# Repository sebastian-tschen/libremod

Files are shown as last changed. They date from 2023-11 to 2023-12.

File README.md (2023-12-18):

# Grind By Weight for Eureka MCI coffee grinder

<p align="center">
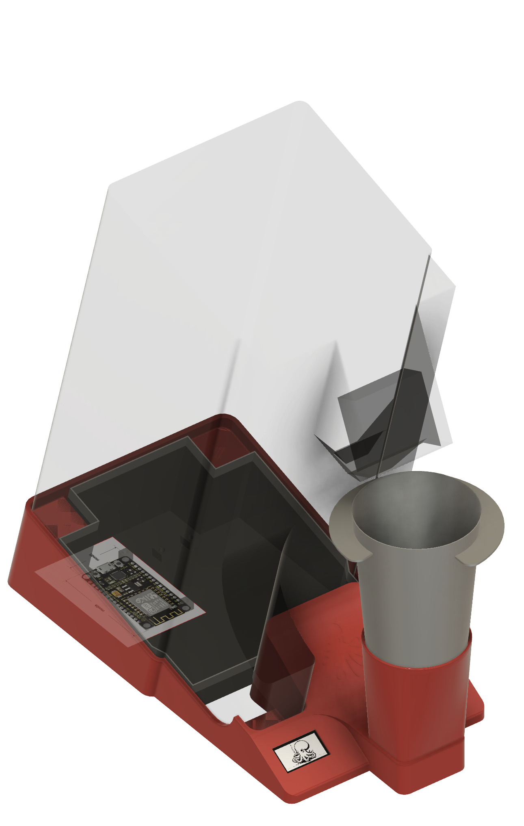
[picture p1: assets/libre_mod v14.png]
  
</p>

This project is based on [the work by Guillaume Besson](https://besson.co/projects/coffee-grinder-smart-scale). I modified it to work with my slightly different grinder and a single core ESP8266 instead of a multi-core ESP32 and added some features to the software

Bill of Material:
-----------------

- Loadcell (mine was 50x10x6mm up to 500g)
- HX711 Load Cell amplifier
- ESP8266 Dev-Board
- 0.96 inch OLED SSD1306 Display
- 4 Cylinder Magnets (6mmx6mm)
- 3D-Printed Parts

### Original electronics of the Eureca MCI

The original electronics slightly differ from the one used bt Guillaume. Mostly the microcontroller operates on a 3.3V instead of 5V. Also, most useful in and outputs where not conviniently accessible via a pinheader.

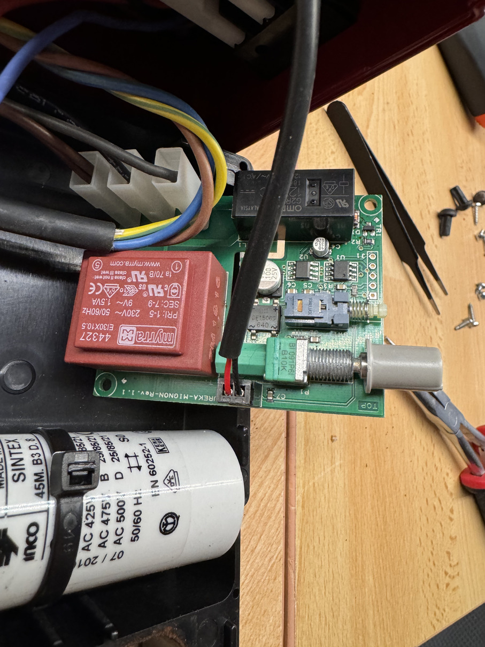
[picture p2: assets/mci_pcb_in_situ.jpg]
Original PCB in-situ


*Original PCB in-situ*

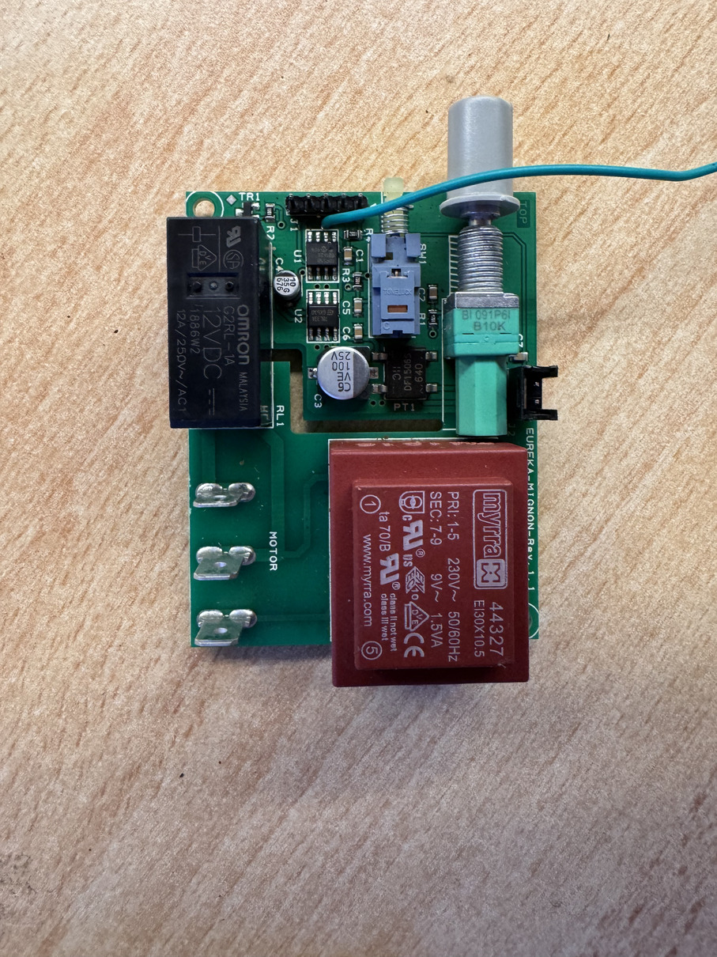
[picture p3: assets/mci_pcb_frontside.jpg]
Original PCB front side


*Original PCB front side*

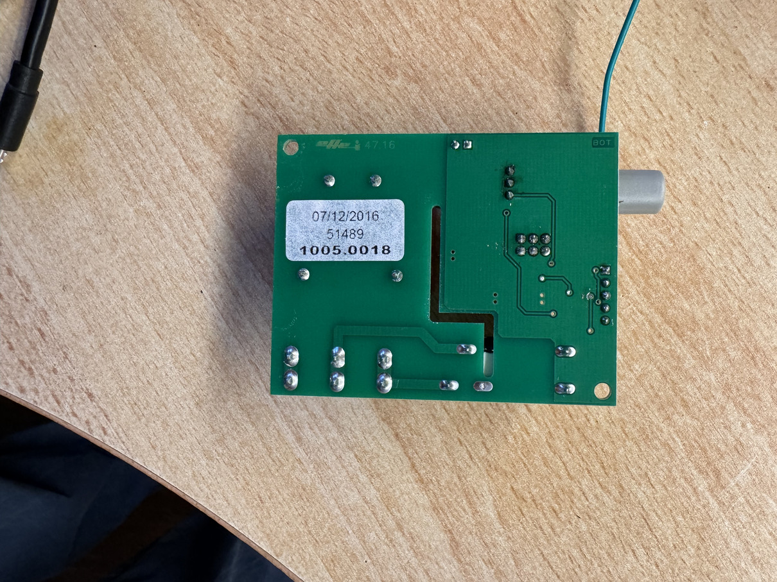
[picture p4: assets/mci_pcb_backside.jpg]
Original PCB back side


*Original PCB back side*

So the first step was revers-engineering the pcb layout

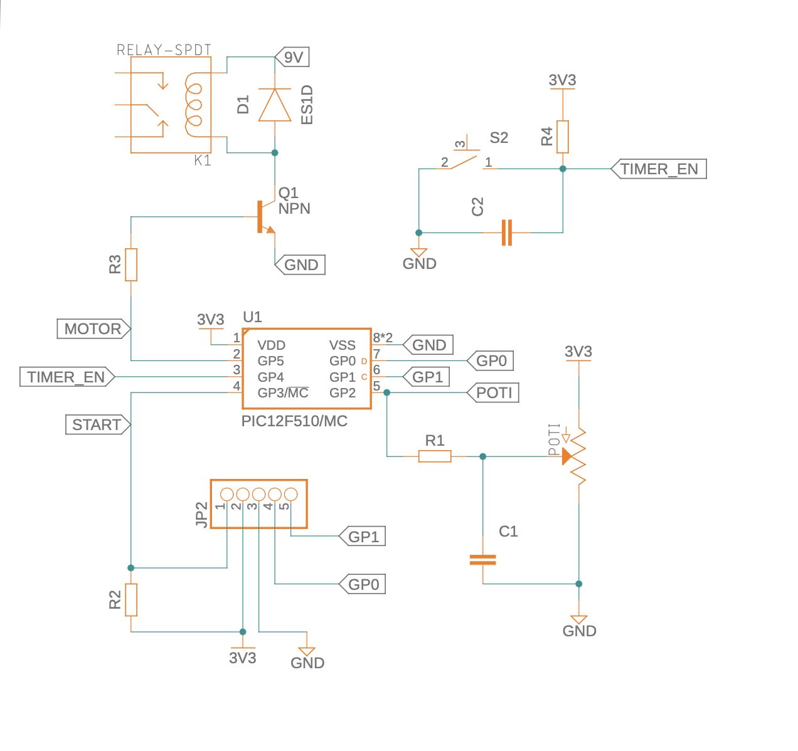
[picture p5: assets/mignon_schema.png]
Original schema for the mignon MCI


*simplified schema of the original MCI pcb*

Most of the electronics where straight forward. I wired the HX711 and loadcell, as well as the oled-screen as required to the ESP-8266 DEV-Board. I took the 3.3V supply from the machine, added two caps for good measure to stabilize the voltage for the esp (which seems to be quite a bit more picky then the pic)
The original electronics board contains a transformer to generate 9V AC, which is then fed to a rectifier and a 3.3V regulator for the tiny PIC12 mcu which controls the machine.

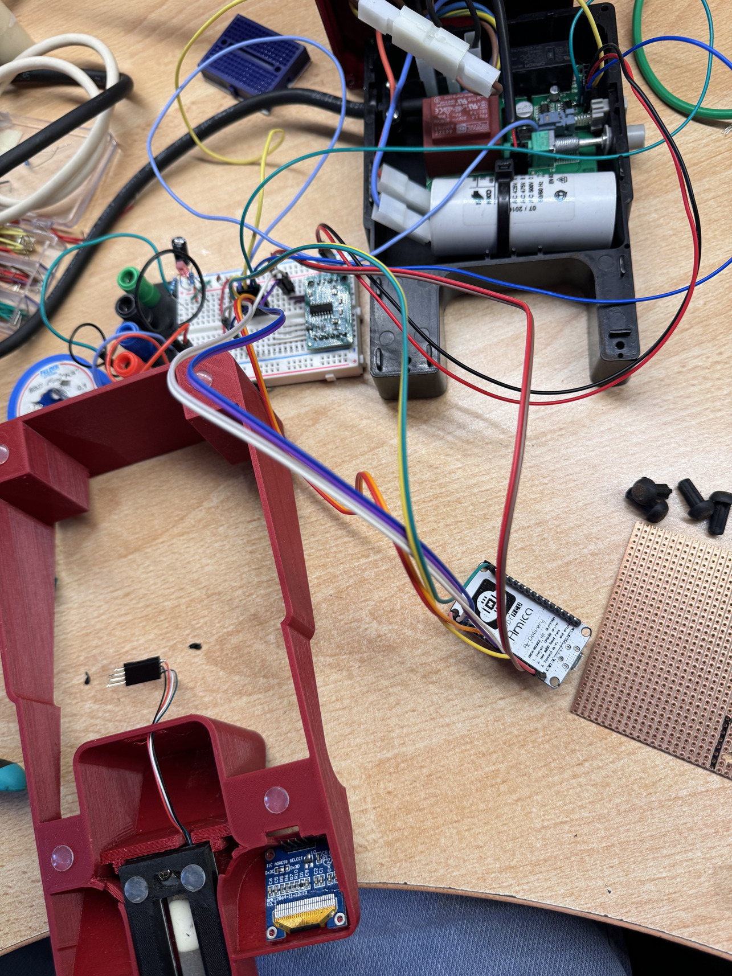
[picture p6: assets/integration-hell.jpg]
integration hell


*the usual chaotic electronics-project*

Interfacing with the old electronics was where I first realized that this might become a bit more of a project.

Directly triggering the relay by setting the `MOTOR` pin high would sink a lot of current into the pic12 microcontroller, which would try to keep it's output low. This would risk damaging the microcontroller at least in the long run.

I could have built a second npn controlled output, directly connected to the 9V supply, but this would mean two more components to solder.

So I opted for just reusing the existing `START` pin of the pic12 and let the original mcu trigger the relay.

This had the effect, that when the timer-enabled switch was turned on, the new mcu wouldn't be able to shut down the grinding process, but I decided to make this a feature instead of a bug.

Thats when I realized i could make use of the existing input-devices provided by the machine. The push-button, to switch between modes, and the potentiometer to select grind-amount. I could sense the state of both, then use the potentiometer position to set the desired weight OR time to grind.

In timing mode, the new mcu would just let the old one make it's job as before, but additionally provide feedback to the user for the grind-time. Something that previously only could be roughly adjusted.

In wight mode, a desired amount of ground coffee is selected with the potentiometer, and the new mcu will hold the 'START' input of the old high until the requested amount is reached

In the end, this is the new electronics-parts I added to the machine

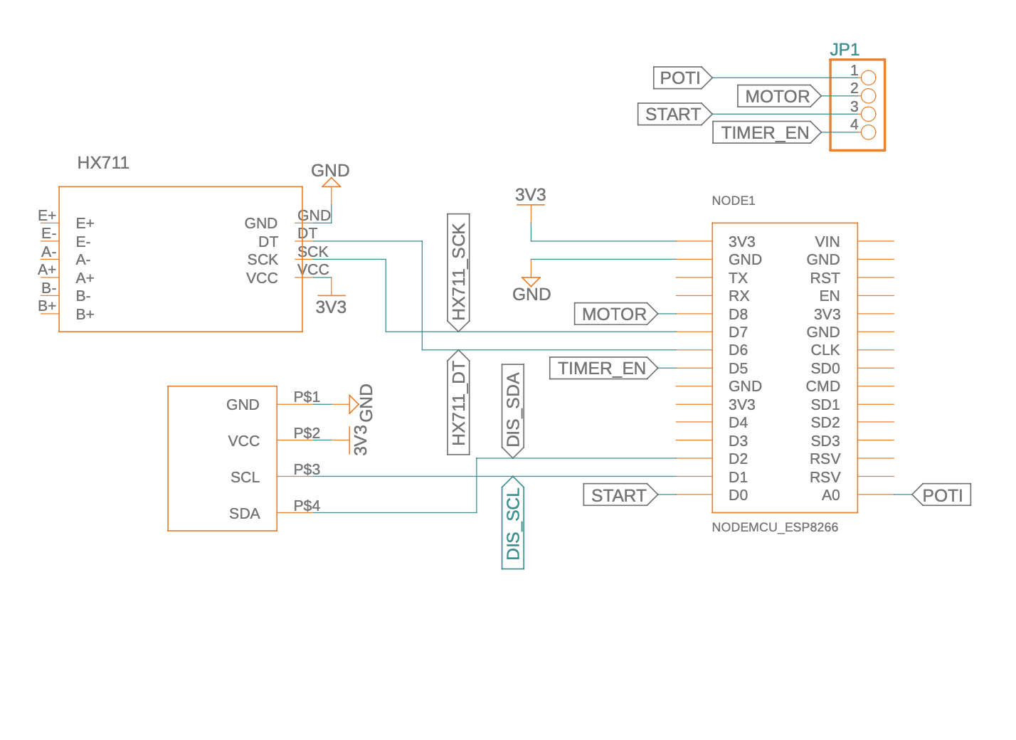
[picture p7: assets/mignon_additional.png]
schema additional electronics


*Schema of additional electronics added for this project*

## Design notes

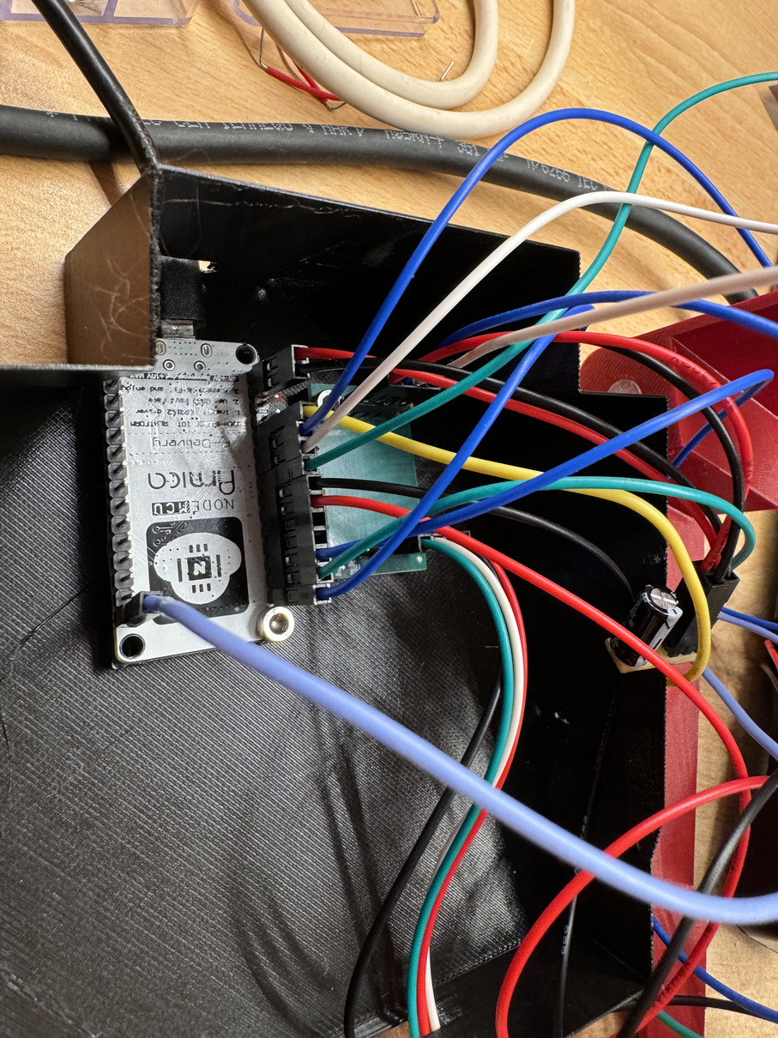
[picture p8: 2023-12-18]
assets/electronics-in-machine.jpg

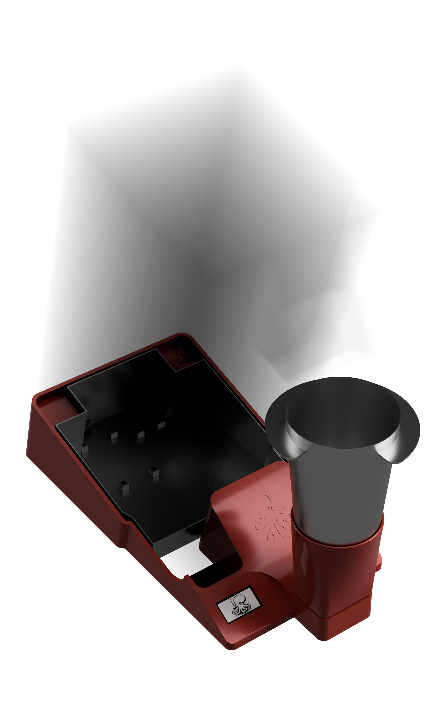
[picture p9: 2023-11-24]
assets/render_large.png

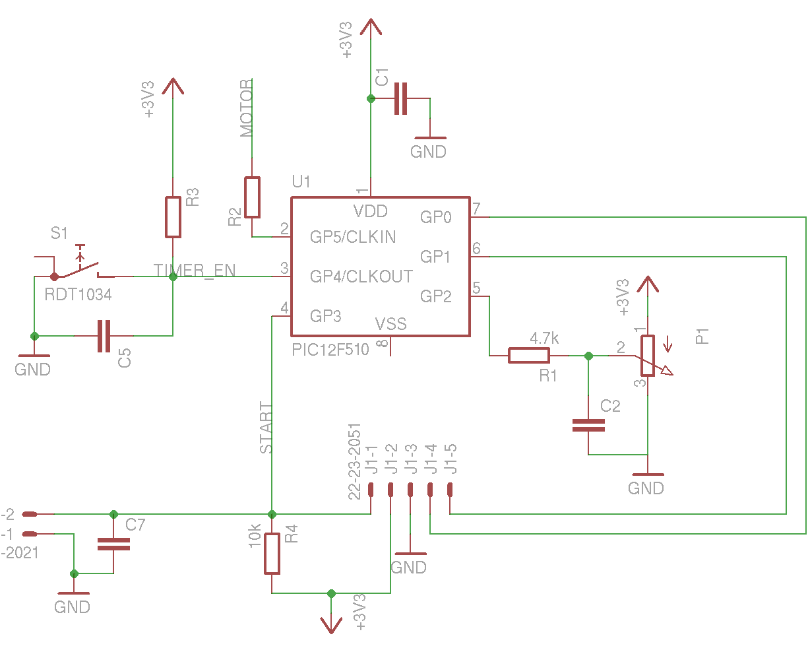
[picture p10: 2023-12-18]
assets/mignon1_1.png

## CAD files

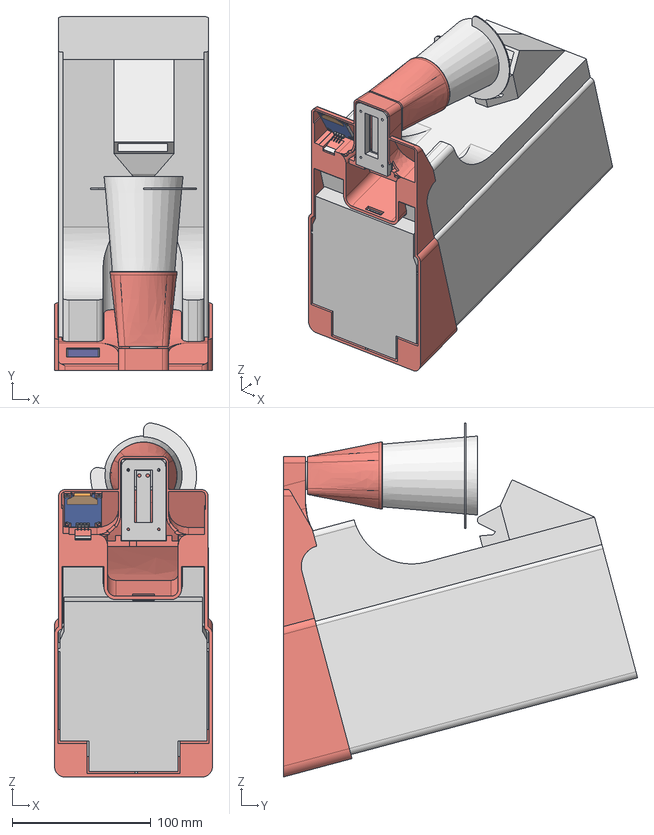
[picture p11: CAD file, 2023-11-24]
3d/libre_mod.step
114.0 x 255.5 x 255.3 mm
new_dosing_cup
load_cell
Mignon MCI (MG50E)
adapter
dosing_cup_auflager
OLED-128x64-0.96
electronics_case

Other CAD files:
3d/libre_mod_no_logo.step

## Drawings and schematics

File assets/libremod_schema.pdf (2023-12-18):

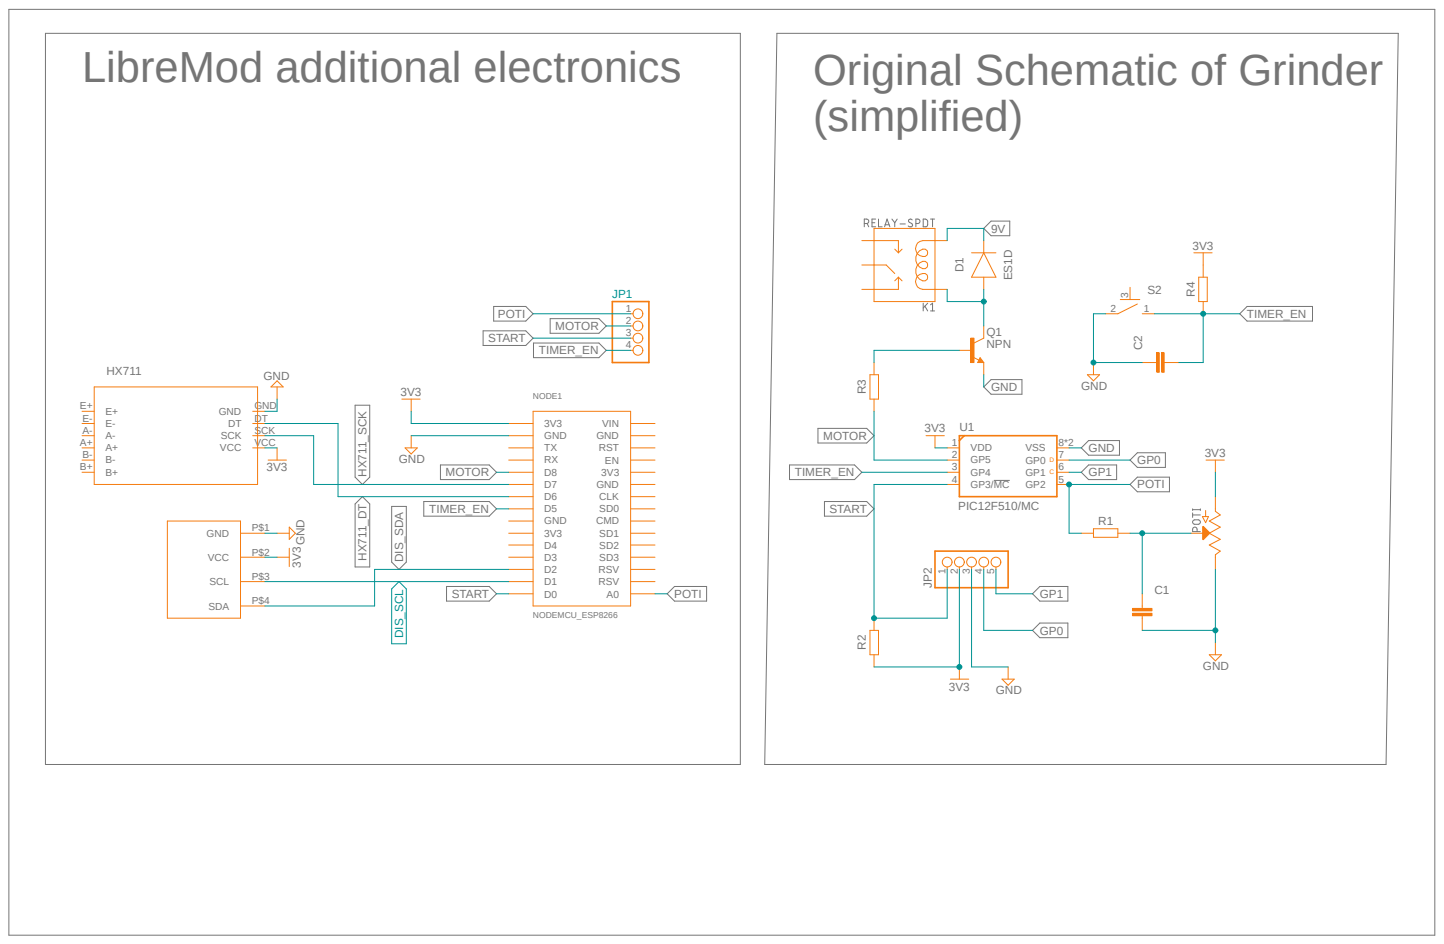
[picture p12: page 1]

Original Schematic of Grinder
(simplified)

GND
SCK SCK DT DT

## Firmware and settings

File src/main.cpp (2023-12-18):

#include <Arduino.h>
#include <ESP8266WiFi.h>

#include "display.hpp"
#include "controller.hpp"


WiFiClient espClient;

void setup() {
  pinMode(GRINDER_START_PIN, INPUT);
  pinMode(GRINDER_SENSE_PIN, INPUT);
  pinMode(GRINDER_MODE_BUTTON_PIN, INPUT);
  setupDisplay();

  Serial.begin(115200);
  while(!Serial){delay(100);}

  setupScale();

}


void loop() {
  updateScale();
  updateDisplay();
  scaleStatusLoop();
}

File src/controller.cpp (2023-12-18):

#include "controller.hpp"
#include <MathBuffer.h>

HX711 loadcell;
SimpleKalmanFilter scaleKalmanFilter(0.2, 0.2, 0.05);

#define ABS(a) (((a) > 0) ? (a) : ((a) * -1))
#define COEFF_A 0.0000192663
#define COEFF_B 0.0046853639
#define COEFF_C 10

double scaleWeight = 0;
unsigned long lastSignificantWeightChangeAt = 0;
unsigned long lastSignificantPotiChangeAt = 0;
unsigned long lastTareAt = 0; // if 0, should tare load cell, else represent when it was last tared
bool scaleReady = false;
int scaleStatus = STATUS_EMPTY;
int currentGrinderMode = GRINDER_MODE_SCALE;
int grindingInProgress = 0;
double cupWeightEmpty = 0;
double totalTimerTime = 0;
unsigned long startedGrindingAt = 0;
unsigned long cupDetectedAt = 0;
unsigned long finishedGrindingAt = 0;
unsigned long stableSince = 0;
MathBuffer<double, 100> weightHistory;
int potiValue = 0;
int lastStablePotiValue = 0;
float coffeeDoseWeight = 14.0;
unsigned long grindmillis = 0;
int errorCode = 0;

void tareScale()
{
  Serial.println("Taring scale");
  loadcell.tare(TARE_MEASURES);
  lastTareAt = millis();
  Serial.println("tara done");
}

void updateScale()
{
  float lastEstimate;
  if (lastTareAt == 0)
  {
    tareScale();
  }
  if (loadcell.wait_ready_timeout(300))
  {
    lastEstimate = scaleKalmanFilter.updateEstimate(loadcell.get_units());
    scaleWeight = lastEstimate;
    weightHistory.push(scaleWeight);
    scaleReady = true;
  }
  else
  {
    Serial.println("HX711 not found.");
    scaleReady = false;
  }
}

void startGrinding()
{
  pinMode(GRINDER_START_PIN, OUTPUT);
  digitalWrite(GRINDER_START_PIN, GRINDER_ON);
}

void stopGrinding()
{
  // avoid draining too much current into pin by making it open/tri-state (high resistance?)
  pinMode(GRINDER_START_PIN, INPUT);
}

void updateGrinderMode()
{
  potiValue = analogRead(A0);
  currentGrinderMode = digitalRead(GRINDER_MODE_BUTTON_PIN);
}

void updateGrindingInProgress()
{
  grindingInProgress = digitalRead(GRINDER_SENSE_PIN);
}

unsigned long extrapolateEndMillis()
{
  unsigned long now = weightHistory.getHeadTimestamp();
  unsigned long offset = now - startedGrindingAt;
  unsigned long durationBegin = now - 4000;
  if (offset < 4000)
  { // we only use data from 4 seconds after grind start
    return 99999999;
  }

  double max = weightHistory.maxSince((int64_t)durationBegin);
  double min = weightHistory.minSince((int64_t)durationBegin);
  double diff = max - min;
  double duration = (double)(4000);
  double slope = (duration) / (diff);
  double missing = coffeeDoseWeight + cupWeightEmpty - max;
  Serial.printf("slope %3.1f ms/g missing %3.1f\n", slope, missing);
  double expectedGrindEnd = ((missing)*slope);
  Serial.printf("end in %3.1fms abs:%lu\n", expectedGrindEnd, now + (long)expectedGrindEnd);
  return (long)expectedGrindEnd;
}

int isCupDetected(void){

  return (ABS(weightHistory.minSince((int64_t)millis() - 200) - CUP_WEIGHT) < CUP_DETECTION_TOLERANCE &&
        ABS(weightHistory.maxSince((int64_t)millis() - 200) - CUP_WEIGHT) < CUP_DETECTION_TOLERANCE) ||
        (ABS(weightHistory.minSince((int64_t)millis() - 200) - CUP_WEIGHT2) < CUP_DETECTION_TOLERANCE &&
        ABS(weightHistory.maxSince((int64_t)millis() - 200) - CUP_WEIGHT2) < CUP_DETECTION_TOLERANCE);
}

void scaleStatusLoop()
{
  double tenSecAvg = weightHistory.averageSince((int64_t)millis() - 10000);
  // Serial.printf("Avg: %f, currentWeight: %f\n", tenSecAvg, scaleWeight);

  if (ABS(tenSecAvg - scaleWeight) > SIGNIFICANT_WEIGHT_CHANGE)
  {
    // Serial.printf("Detected significant change: %f\n", ABS(avg - scaleWeight));
    lastSignificantWeightChangeAt = millis();
  }

  if (ABS(lastStablePotiValue - potiValue) > SIGNIFICANT_POTI_CHANGE)
  {
    lastStablePotiValue = potiValue;
    lastSignificantPotiChangeAt = millis();
    coffeeDoseWeight = lastStablePotiValue*lastStablePotiValue*COEFF_A + lastStablePotiValue*COEFF_B + COEFF_C;
    totalTimerTime = (potiValue * (9.530318) + 4229.09) / 1000;
  }

  if (scaleStatus == STATUS_EMPTY)
  {
    updateGrinderMode();
    updateGrindingInProgress();

    if (millis() - lastTareAt > TARE_MIN_INTERVAL && ABS(tenSecAvg) > 0.2 && tenSecAvg < 3 && scaleWeight < 3)
    {
      // tare if: not tared recently, more than 0.2 away from 0, less than 3 grams total (also works for negative weight)
      tareScale();
      lastTareAt = 0;
    }
    // check if someone pressed a button on the grinder an we are currently grinding
    if (grindingInProgress)
    {
      if (currentGrinderMode == GRINDER_MODE_TIMER)
      {
        startedGrindingAt = millis();
        cupWeightEmpty = weightHistory.averageSince((int64_t)millis() - 500);
        scaleStatus = STATUS_TIMER_GRINDING_IN_PROGRESS;
        Serial.println("Externally started Timer Grind");
        return;
      }
      else
      {
        if (scaleWeight > MIN_CUP_WEIGHT)
        { // if we have currently something cup like on the scale, then start a regular-weight based grind
          Serial.println("Starting grinding due to button-press");
          cupWeightEmpty = weightHistory.averageSince((int64_t)millis() - 500);
          scaleStatus = STATUS_SCALE_GRINDING_IN_PROGRESS;
          startedGrindingAt = millis();
          startGrinding();
          return;
        }
        else
        { // if there ist nothing substantial on the scale, start a manual grindinf process
          Serial.println("Starting manual grinding");
          scaleStatus = STATUS_MANUAL_GRINDING_IN_PROGRESS;
          cupWeightEmpty = 0;
          startedGrindingAt = millis();
          return;
        }
      }
    }
    // see if we can detect a cup
    if (isCupDetected())
    {
      scaleStatus=STATUS_SCALE_CUP_DETECTED;
      cupDetectedAt = millis();
      Serial.println("cup detected");
      return;
    }
  }
  else if (scaleStatus == STATUS_SCALE_GRINDING_IN_PROGRESS)
  {
    if (!scaleReady)
    {
      Serial.println("Failed because scale not ready");
      stopGrinding();
      scaleStatus = STATUS_GRINDING_FAILED;
      errorCode = SCALE_NOT_READY;
      return;
    }

    if (millis() - startedGrindingAt > MAX_GRINDING_TIME)
    {
      Serial.println("Failed because grinding took too long");
      stopGrinding();
      scaleStatus = STATUS_GRINDING_FAILED;
      errorCode = GRINDING_TOOK_TOO_LONG;
      return;
    }

    if (
        millis() - startedGrindingAt > 4000 &&                               // started grinding at least 4s ago
        scaleWeight - weightHistory.firstValueOlderThan(millis() - 4000) < 1 // less than a gram has been ground in the last 4 second
    )
    {
      Serial.println("Failed because no change in weight was detected");
      stopGrinding();
      scaleStatus = STATUS_GRINDING_FAILED;
      errorCode = NO_WEIGHT_CHANGE;
      return;
    }
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

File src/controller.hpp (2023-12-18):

#pragma once

#include <SimpleKalmanFilter.h>
#include <MathBuffer.h>
#include "HX711.h"

#define STATUS_EMPTY 0
#define STATUS_SCALE_GRINDING_IN_PROGRESS 1
#define STATUS_TIMER_GRINDING_IN_PROGRESS 2
#define STATUS_MANUAL_GRINDING_IN_PROGRESS 3
#define STATUS_SCALE_GRINDING_FINISHED 4
#define STATUS_TIMER_GRINDING_FINISHED 5
#define STATUS_MANUAL_GRINDING_FINISHED 6
#define STATUS_GRINDING_FAILED 7
#define STATUS_SCALE_CUP_DETECTED 8

#define WEIGHT_TOO_LOW 1
#define NO_WEIGHT_CHANGE 2
#define GRINDING_TOOK_TOO_LONG 3
#define SCALE_NOT_READY 4



#define GRINDER_MODE_TIMER 0
#define GRINDER_MODE_SCALE 1

#define CUP_WEIGHT 63.5
#define CUP_WEIGHT2 58.5
#define CUP_DETECTION_TOLERANCE 2 // 1 gram tolerance above or bellow cup weight to detect it

#define MIN_CUP_WEIGHT 20 // min weight on scale to be considered a cup

#define LOADCELL_DOUT_PIN D6
#define LOADCELL_SCK_PIN D7

#define LOADCELL_SCALE_FACTOR -714.6

#define TARE_MEASURES 20 // use the average of measure for taring
#define SIGNIFICANT_WEIGHT_CHANGE 5 // 5 grams changes are used to detect a significant change
#define SIGNIFICANT_POTI_CHANGE 2 // 5 grams changes are used to detect a significant change
#define MAX_GRINDING_TIME 40000 // 40 seconds diff
#define EXPECTED_DELAY 850 // number of ms to stop before extrapolated finish time
#define GRINDING_FAILED_WEIGHT_TO_RESET 500 // force on balance need to be measured to reset grinding

#define GRINDER_START_PIN D0

#define GRINDER_ON 0
#define GRINDER_OFF 1

#define GRINDER_MODE_BUTTON_PIN D5

#define GRINDER_SENSE_PIN D8

#define TARE_MIN_INTERVAL 10 * 1000 // auto-tare at most once every 10 seconds

extern double scaleWeight;
extern unsigned long lastSignificantWeightChangeAt;
extern unsigned long lastSignificantPotiChangeAt;
extern unsigned long lastTareAt;
extern bool scaleReady;
extern int scaleStatus;
extern int currentMode;
extern double cupWeightEmpty;
extern double totalTimerTime;
extern int currentGrinderMode;
extern unsigned long startedGrindingAt;
extern unsigned long cupDetectedAt;
extern unsigned long finishedGrindingAt;
extern unsigned long stableSince;
extern int potiValue;
extern float coffeeDoseWeight;
extern unsigned long grindmillis;
extern int errorCode;
extern MathBuffer<double, 100> weightHistory;

void updateScale();
void scaleStatusLoop();
void setupScale();
void detectTimeGrind();
